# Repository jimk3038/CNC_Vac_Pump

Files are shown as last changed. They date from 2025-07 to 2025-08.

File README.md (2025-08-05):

# CNC Vacuum Pump Controller

This repo goes along with the following YouTube video:
https://youtu.be/Fw-1sRhIoUw

Update Video:
https://youtu.be/3FdK16Jd_hk

CNC Vacuum Pump Controller
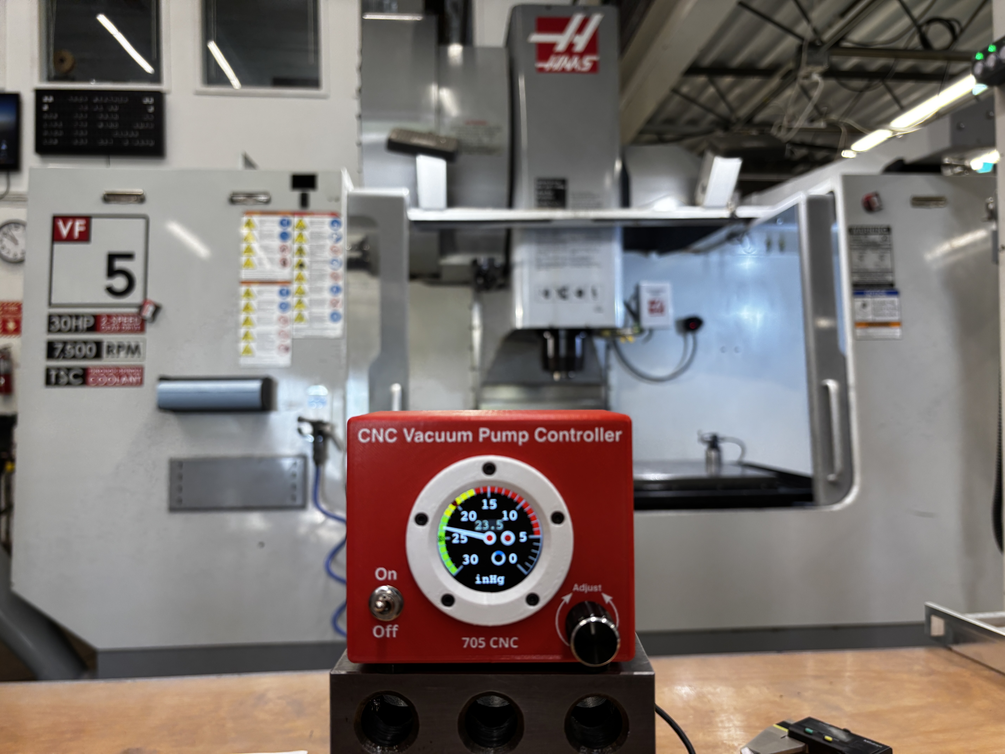
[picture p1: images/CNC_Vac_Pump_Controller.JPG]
CNC Vacuum Pump Controller


Everything needed to get up and running, in terms of CNC Vacuum plates and chucks is covered here.  Specifically, the actual vacuum pump controller is covered.

Vacuum Plate Example (see CAD/Vacuum_Plate_v2.STEP)
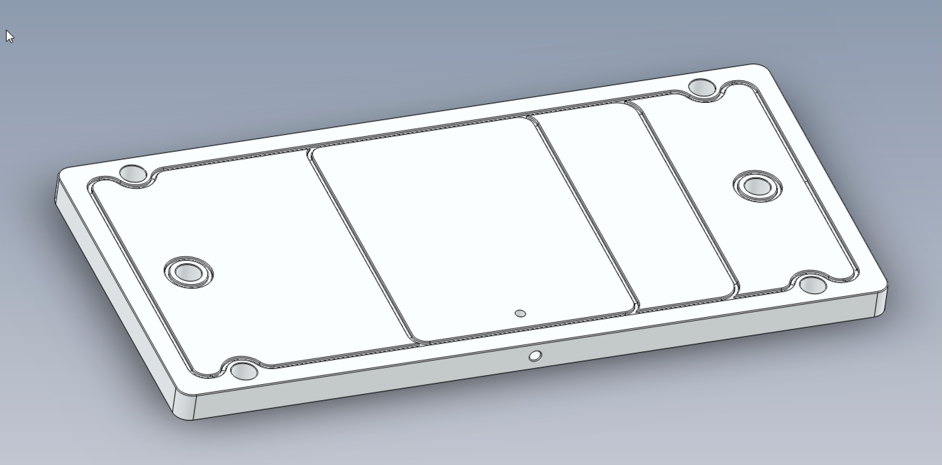
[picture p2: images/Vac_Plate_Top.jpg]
Vacuum Plate Example


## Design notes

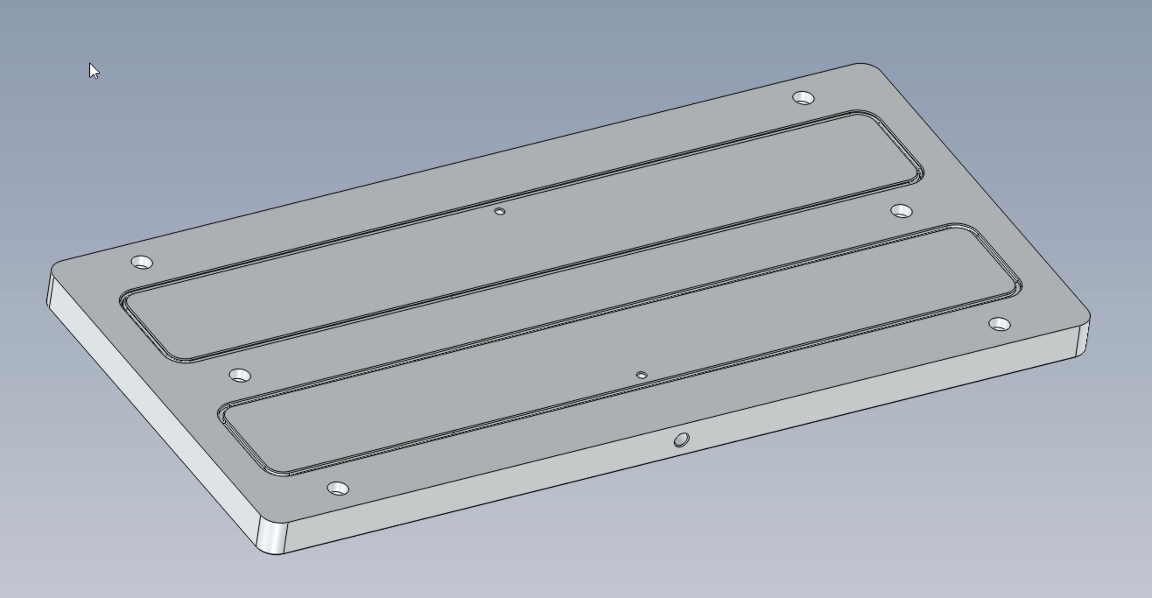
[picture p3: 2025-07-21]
images/Vac_Plate_Bottom.jpg

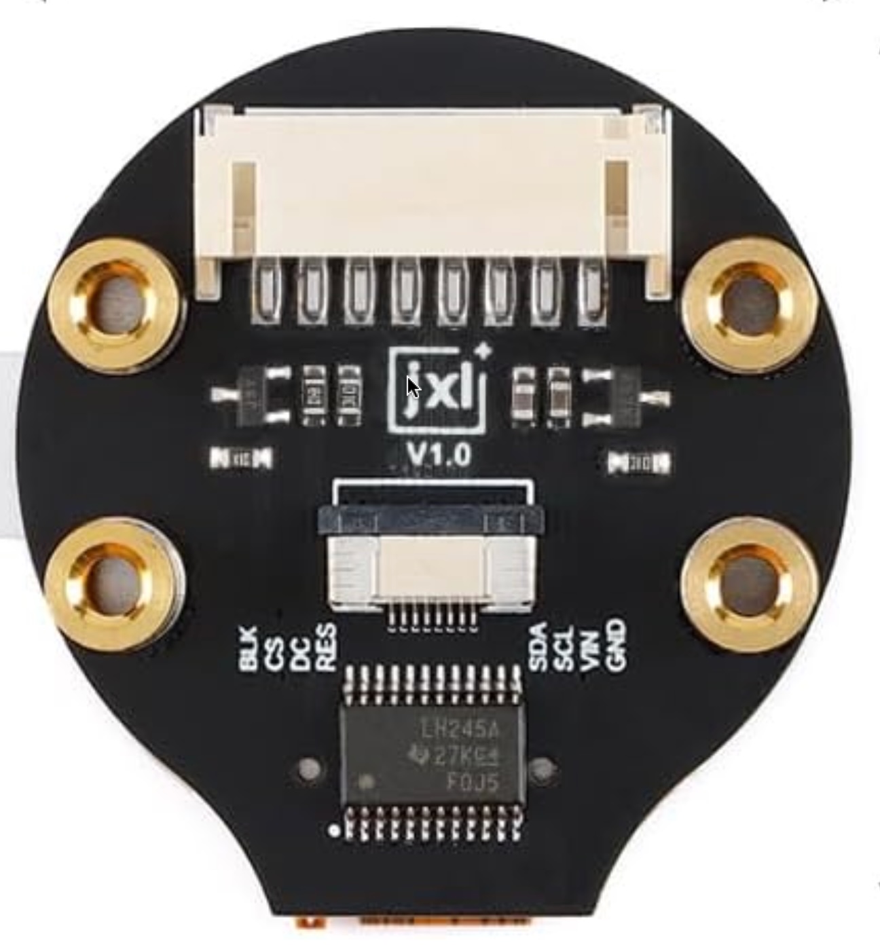
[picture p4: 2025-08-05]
images/LCD.jpg

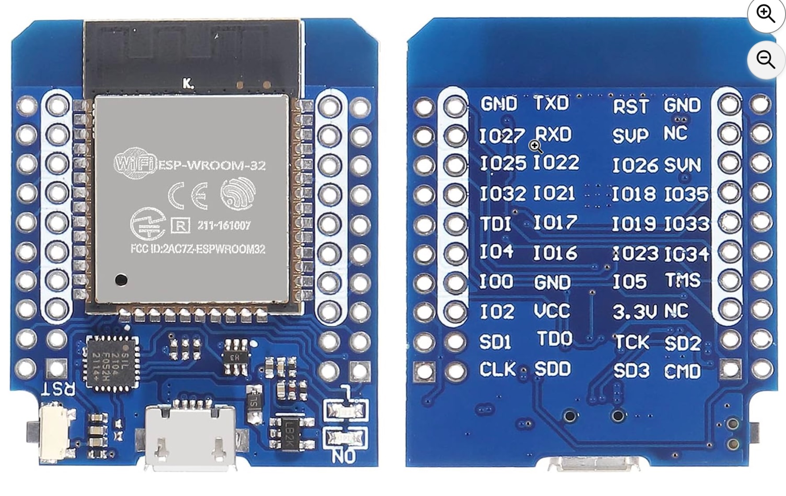
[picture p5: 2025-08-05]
images/D1_Mini32_ESP32.jpg

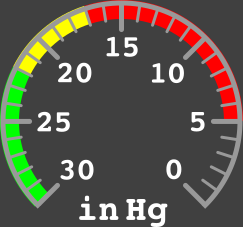
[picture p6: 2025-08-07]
source/SquareLine_VacDisp/assets/Small_Gauge_Scale_.png

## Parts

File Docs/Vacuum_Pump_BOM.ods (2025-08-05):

 | CNC Vacuum Pump Controller BOM
Supplier | Part Num | Description | Min Quantity | Unit Price | Total
Amazon | https://www.amazon.com/dp/B0CB3V1366 | LCD | 3 | $6.33 | $19.00
Amazon | https://www.amazon.com/dp/B08PNWB81Z | ESP32 | 5 | $6.00 | $30.00
Amazon | https://www.amazon.com/dp/B0C6Q67V97 | Encoder | 6 | $1.50 | $9.00
Amazon | https://www.amazon.com/dp/B07QGDDTWJ | Switch | 8 | $0.96 | $7.66
 |  | PLA Plastic | 1 | $4.00 | $4.00 | Unit Total: | $60.19
Amazon | https://www.amazon.com/dp/B00E0NTPP4 | Relay1 | 1 | $6.80 | $6.80 | Total: | $118.06
 |  | Relay2 | 1 | $8.00 | $8.00
 |  | Wire | 1 | $2.00 | $2.00
Mouser | 841-MPXV4115VC6U | Sensor | 1 | $23.10 | $23.10
 |  | Sensor Adapter Hose | 15 | $0.50 | $7.50
 |  | Printing | 1 | $1.00 | $1.00
 |  | Extra Stuff
 |  | Shopify | 1 | $6.00 | $6.00
 |  | Packaging | 1 | $2.00 | $2.00
 |  | Shipping | 1 | $5.00 | $5.00

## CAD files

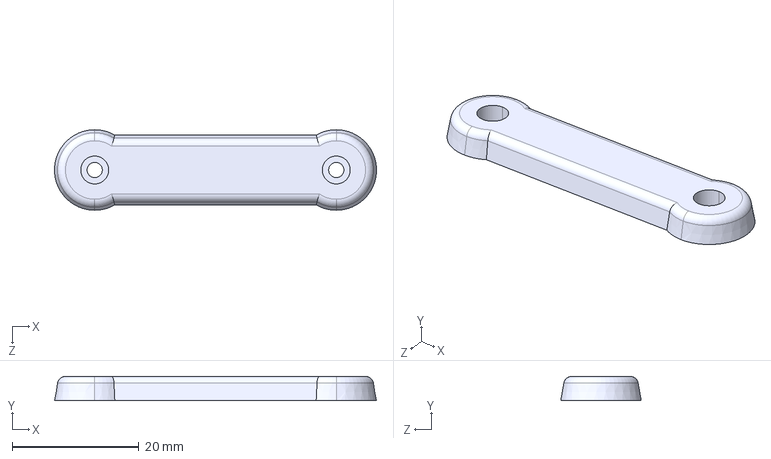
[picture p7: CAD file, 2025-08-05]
CAD/Rubber_Foot_Strip.STEP
50.8 x 3.81 x 12.7 mm

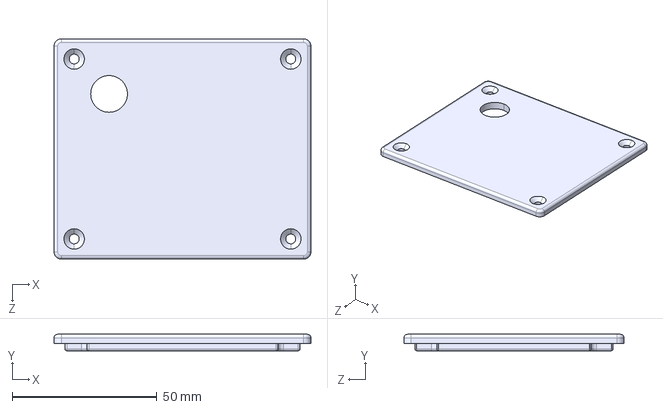
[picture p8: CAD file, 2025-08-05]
CAD/Back_Cover.STEP
88.9 x 5.71 x 76.2 mm

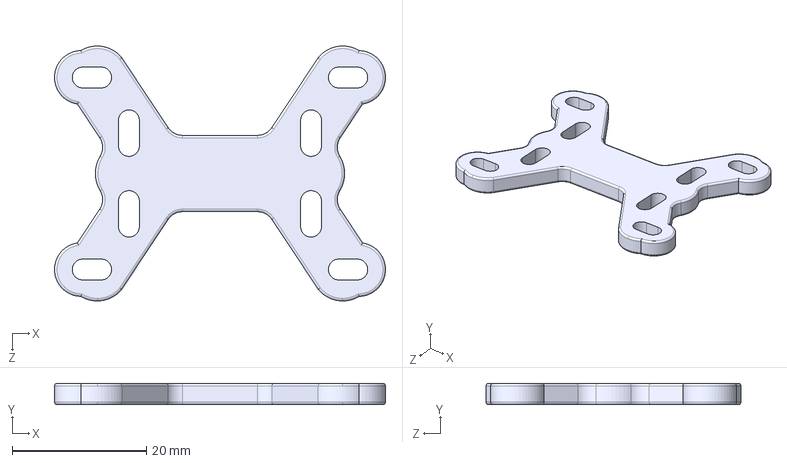
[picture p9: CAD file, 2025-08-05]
CAD/LCD_Support_JXL_.STEP
49.2 x 3.17 x 37.9 mm

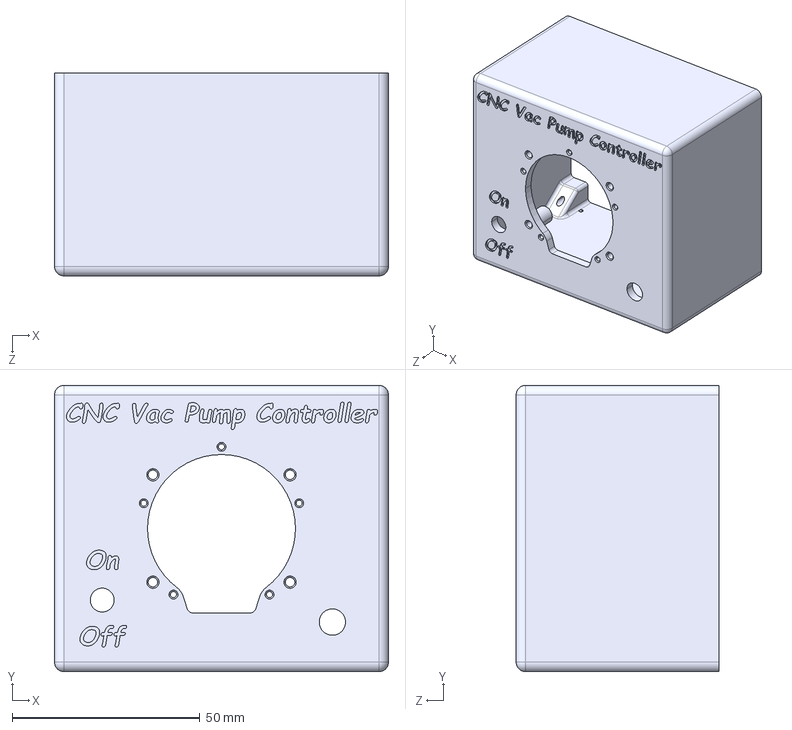
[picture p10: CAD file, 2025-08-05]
CAD/Enclosure.STEP
88.9 x 76.2 x 54.0 mm

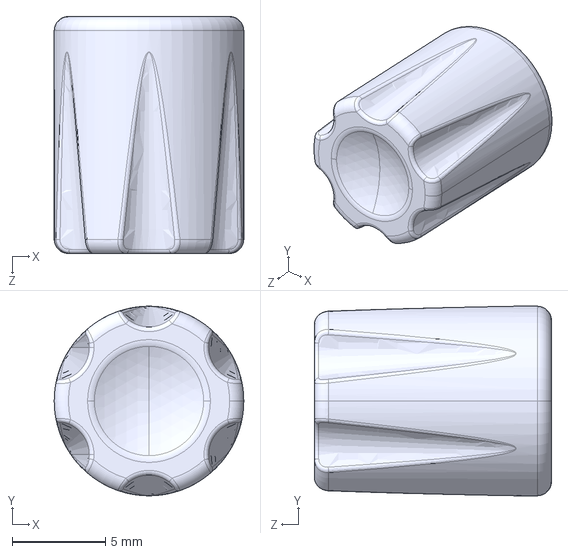
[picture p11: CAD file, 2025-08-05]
CAD/Knob.STEP
10.2 x 10.2 x 12.7 mm

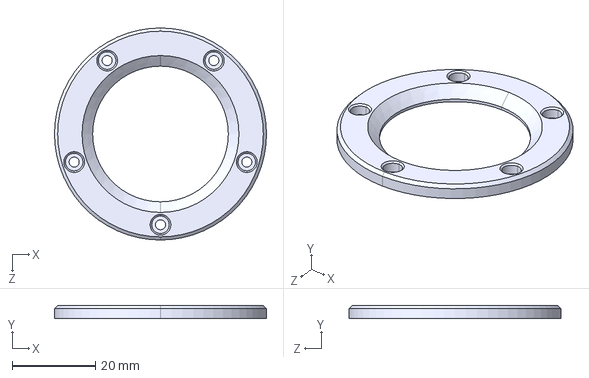
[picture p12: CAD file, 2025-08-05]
CAD/Bezel.STEP
50.8 x 3.17 x 50.8 mm

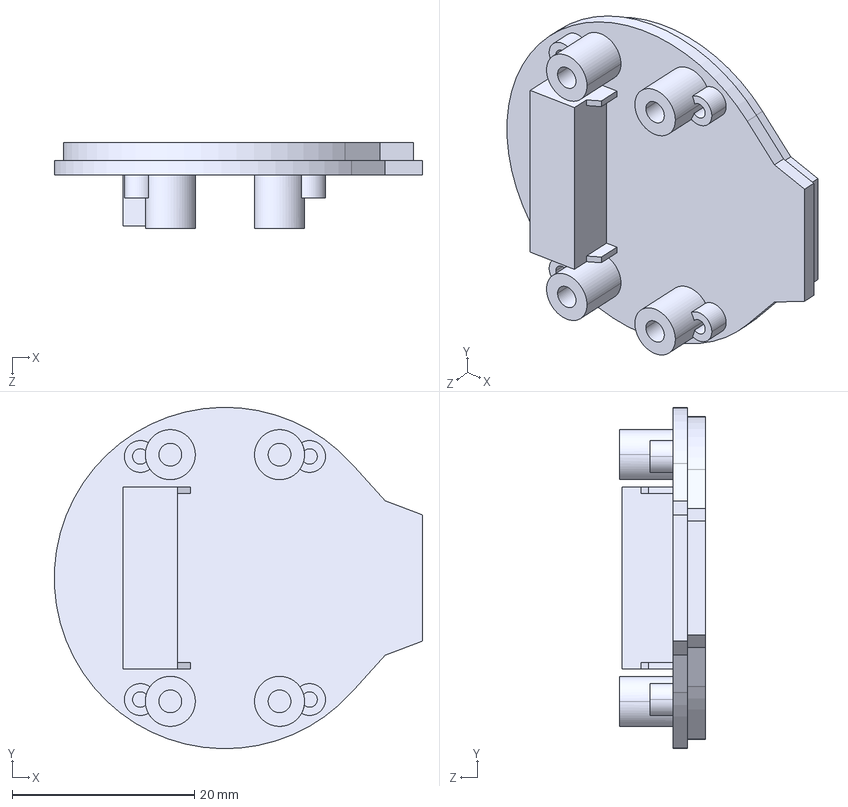
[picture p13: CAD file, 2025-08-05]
CAD/Round_LCD_1pt28in_JKL.STEP
40.4 x 37.5 x 9.50 mm

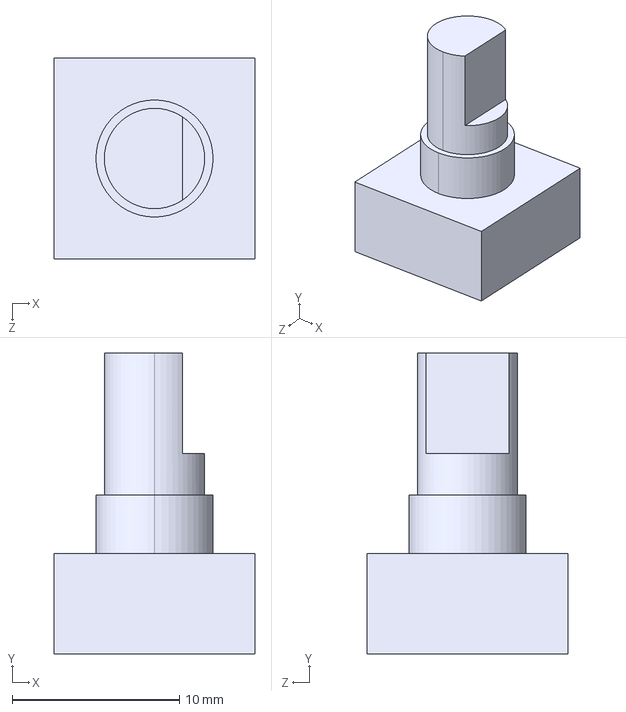
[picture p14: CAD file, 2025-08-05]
CAD/Encoder.STEP
12.0 x 18.0 x 12.0 mm

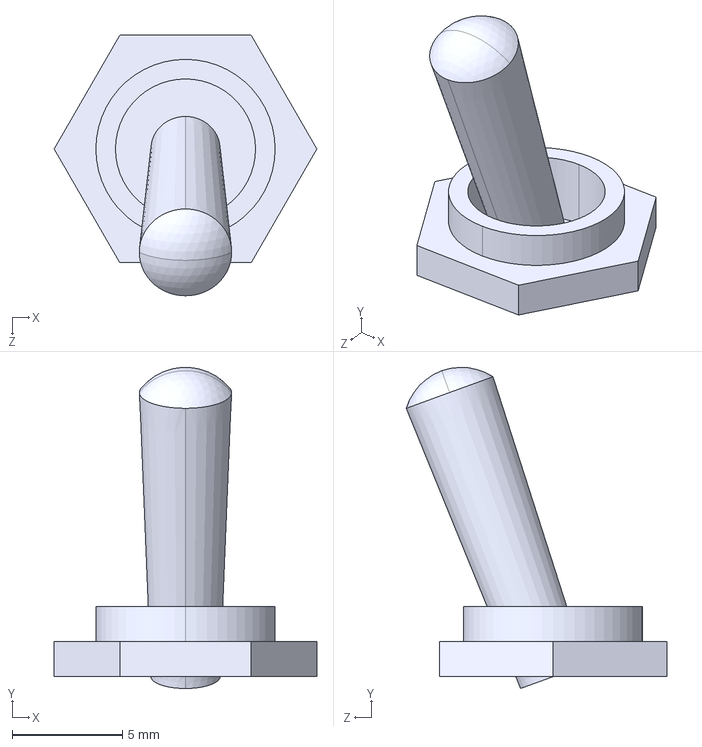
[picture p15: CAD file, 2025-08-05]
CAD/Toggle_Switch.STEP
11.9 x 14.6 x 11.8 mm

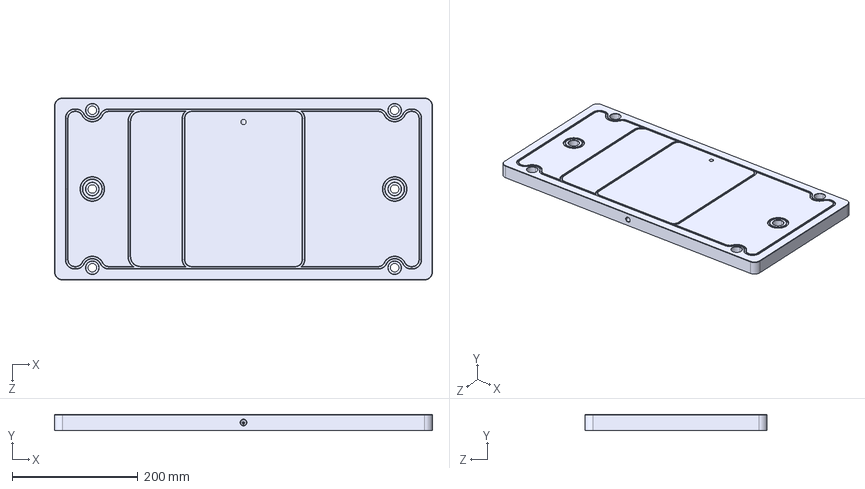
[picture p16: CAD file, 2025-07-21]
CAD/Vacuum_Plate_v2.STEP
600.1 x 25.4 x 288.9 mm

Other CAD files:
CAD/Vacuum_Plate_v2.SLDPRT

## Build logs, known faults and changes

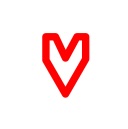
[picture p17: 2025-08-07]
source/SquareLine_VacDisp/assets/red_bug.jpg

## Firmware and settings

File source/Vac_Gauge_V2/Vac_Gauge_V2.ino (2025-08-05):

//
// CNC Vacuum Pump Controller
//
// See "notes.h" for documentation.
//

// Setup the vacuum high and low default thresholds before including "encoder.h".
// The values are in "inHg * 10".  So, a value of 200 is really 20.0inHg.
int16_t red=200, grn=250;

#include "encoder.h"

// Comment out the next line to build program WITHOUT the LCD / GUI interface.
// With the GUI, the ESP32 will just switch the pump on/off at the threshold
// points.  You will need to recompile the code to change the switch points.
#define USE_GUI

#ifdef USE_GUI
  #include <TFT_eSPI.h>
  #include <lvgl.h>
  #include "src/ui_lvgl/ui.h"

  // Waveshare 1.28in Round LCD
  static const uint16_t screenWidth  = 240;
  static const uint16_t screenHeight = 240;

  static lv_disp_draw_buf_t draw_buf;
  static lv_color_t buf[ screenWidth * 10 ];

  TFT_eSPI tft = TFT_eSPI(screenWidth, screenHeight); // TFT Instance
  lv_disp_drv_t disp_drv;
  bool guiActive = true;
#else
  bool guiActive = false;
#endif


const int ledPin = 2;             // Debug LED on ESP32 board.
const int vacSensorPin = 35;      // Analog Input Pin for Vacuum Sensor
const int sensorPwrPin = 4;       // Dummy pin provides power for Vac Sensor
const int vacPumpPin = 26;        // Output to Vacuum Pump Relay
const int vacAlarmPin = 21;       // Output to Alarm Relay

// Relays are active low.  Enum makes for a nice way to control them, I think.
enum relayType{ On = 0, Off = 1 };

uint16_t getFilteredVacSensor();
int cmpfunc (const void * a, const void * b);
void printTypes();
void startGUI();

// Timers used with millis().
uint64_t tm, lv_tm1, lv_tm2, lv_tm3, tm4;

#ifdef USE_GUI

  // LCD Display Flushing for LVGL
  // ============================================================================
  void my_disp_flush( lv_disp_drv_t *disp, const lv_area_t *area, lv_color_t *color_p ) {
      uint32_t w = ( area->x2 - area->x1 + 1 );
      uint32_t h = ( area->y2 - area->y1 + 1 );

      tft.startWrite();
      tft.setAddrWindow( area->x1, area->y1, w, h );
      tft.pushColors( ( uint16_t * )&color_p->full, w * h, true );
      tft.endWrite();

      lv_disp_flush_ready( disp );
  }

  // Use Arduino millis() as tick source.
  static uint32_t my_tick(void) {
      return millis();
  }
#endif

// ============================================================================
void setup() {
    Serial.begin( 115200 );

    pinMode( sensorPwrPin, OUTPUT );      // Dummy 3.3V to Vac Sensor
    digitalWrite( sensorPwrPin, HIGH );
    pinMode( vacSensorPin, INPUT );       // Vac Analog Sensor Input    

    pinMode( ledPin, OUTPUT );            // ESP32 Board LED
    digitalWrite( ledPin, HIGH );

    pinMode( vacPumpPin, OUTPUT );        // Outputs to dual realy board.
    digitalWrite( vacPumpPin, Off );
    pinMode( vacAlarmPin, OUTPUT );
    digitalWrite( vacAlarmPin, Off );

    xTaskCreate(
      encTask,		  // My Simple Encoder Task
      "Encoder",		// Task Name String
      10000,			  // Stack size in bytes.
      NULL,			    // Parameter passed as input of the task.
      1,				    // Priority of the task.  Higher Num = Higher Priority
      NULL);			  // Task handle.

    Serial.printf("\nCNC Vac Pump Controller:\n");
    #ifdef USE_GUI
      startGUI();     // Init and startup GUI display here.
      Serial.printf("\tLVGL: %d.%d.%d\n",
        lv_version_major(), lv_version_minor(), lv_version_patch() );
    #endif
    Serial.printf( "Setup Done\n" );

    // Init the timers so they are staggered.  This keeps them from happening 
    // at the same time.  Also, to keep the stagger working, jump the timer(s) forward 
    // on multiples of 5 milliseconds.
    tm = millis();
    lv_tm1 = tm + 1;
    lv_tm2 = tm + 2;
    lv_tm3 = tm + 3;
    tm4 = tm + 4;
}

// ============================================================================
void loop() {
  static int ang;
  char sVal[30];
  static bool ledFlg = true;
  static int cnt_old;
  static int vacSensor, vacVal;

  #ifdef USE_GUI
    // This should be moved to a high priority FreeRTOS task.
    if( guiActive && lv_tm1 < millis() ) {      
      lv_tick_inc( 5 );           // Update GUI animations.
      lv_tm1 += 5;
    }

    if( guiActive && lv_tm2 < millis() ) {
      lv_timer_handler();         // Update GUI every 5ms.
      lv_tm2 += 5;
    }
    
    // Update vacuum label and needle angle.
    if( guiActive && millis() > lv_tm3 ) {
      // lv_tm3 += 45;
      lv_tm3 += 15;
      // int vacSensor = analogRead( VAC_SENSOR );
      // vacSensor = getFilteredVacSensor();
    
      sprintf( sVal, "%0.1f", vacVal / 10.0 );
      lv_label_set_text( ui_vacLabel, sVal );

      ang = map( vacSensor, 0, 4096, 0, 2700 );
      lv_img_set_angle( ui_Needle, ang );

      // Pump On
      if( vacVal <= red )
        lv_obj_clear_flag( ui_ledRedImage, LV_OBJ_FLAG_HIDDEN );

      // Pump Off
      if( vacVal >= grn )
        lv_obj_add_flag( ui_ledRedImage, LV_OBJ_FLAG_HIDDEN );
    }

      // On encoder counts change...
    if( guiActive && cnt != cnt_old ) {
      // Serial.printf("Cnt: %d   Red: %d   Grn: %d\n", cnt, red, grn );
      // In case one bug is getting pushed by the other bug, update both bugs.
      uint16_t redBugAng = map( red, 300, 0, -1350, 1350 );
      lv_img_set_angle( ui_redBugImg, redBugAng );
      uint16_t grnBugAng = map( grn, 300, 0, -1350, 1350 );
      lv_img_set_angle( ui_grnBugImg, grnBugAng );
    }
    cnt_old = cnt;
  #endif

  // Toggle Board Debug LED - just to show some life.
  if( millis() > tm ) {
    tm += 250;
    ledFlg ^= true;                   // Toggle flag.
    digitalWrite( ledPin, ledFlg );
  }

  // Read Vacuum sensor and update the pump and alarm outputs.
  if( tm4 < millis() ) {
    tm4 += 10;
    
    vacSensor = getFilteredVacSensor();
    vacVal = map( vacSensor, 0, 4090, 300, 0 );

    if( vacVal <= red )  digitalWrite( vacPumpPin, On );
    if( vacVal >= grn )  digitalWrite( vacPumpPin, Off );

    // ToDo: Add code to drive the alarm output too.
  }
}



// Size of median filter for incoming analog values.
#define NUM_VAC_VALUES	15
#define NUM_VAC_AVG     15

// Get Filter Vacuum Sensor: Reads a new value from the analog input pis.
// The new value is added to a median filter who's output is then averaged.
// The median filter gets rid of "flyer" values, and then, the averaging
// smooths just a bit.  The downside to all this filtering, of course, is a 
// delay in seeing real changes.  In other words, it takes some time for 
// a large jump in the actual value to percolate through the filters.
// However, in this application, slow moving values are the norm!
// ============================================================================
uint16_t getFilteredVacSensor( ) {
  static uint16_t vacValuesRaw[ NUM_VAC_VALUES ];       // Ring Buffer of Raw Values
  static uint16_t vacValuesSorted[ NUM_VAC_VALUES ];    // Sorted Copy of Ring Buff
  static uint8_t vacValIndex = 0;                       // Current Index into Ring Buffer
	static uint32_t avgVac = 0;                           // Running Average
  
  // Overwritten oldest val in the ring buffer with new analog value.
	vacValuesRaw[ vacValIndex ] = analogRead( vacSensorPin );
	vacValIndex = ++vacValIndex > NUM_VAC_VALUES ? 0 : vacValIndex;   // If needed, wrap index.

	// Copy the unsorted raw values and overwrite the old sorted values.
	memcpy( vacValuesSorted, vacValuesRaw, sizeof(uint16_t) * NUM_VAC_VALUES );

	// QSort the values so we can find the 'median' value in the sorted list.
  // Note, QSort is super fast and efficient - truly magical and worth the effort.
	qsort( vacValuesSorted, NUM_VAC_VALUES, sizeof(uint16_t), cmpfunc);

  // Take the middle value from the sorted array - this is the 'median' value.
  // Compute an average of that median value to smooth it.
	avgVac = (avgVac * (NUM_VAC_AVG - 1) + vacValuesSorted[ NUM_VAC_VALUES / 2 ]) / NUM_VAC_AVG;
	return avgVac;
}

// Used by the QSort function to compare two values.
// ============================================================================
int cmpfunc (const void * a, const void * b) {
	if( *(int*)a > *(int*)b ) return 1;
	else if( *(int*)a == *(int*)b ) return 0;
	else return -1;
}

// Everything needed to startup the LCD display using TFT_eSPI and LVGL.
// ============================================================================
#ifdef USE_GUI
void startGUI( ) {

  // If USE_GUI is not defined then this function does nothing.
    lv_init();

    tft.begin();            // TFT Init
    tft.setRotation( 0 );   // No landscape or flipped needed.

    lv_disp_draw_buf_init( &draw_buf, buf, NULL, screenWidth * 10 );

    // Initialize the display
    lv_disp_drv_init( &disp_drv );
    disp_drv.hor_res = screenWidth;
    disp_drv.ver_res = screenHeight;
    disp_drv.flush_cb = my_disp_flush;
    disp_drv.draw_buf = &draw_buf;
    lv_disp_drv_register( &disp_drv );

    ui_init();
}
#endif

// // Debugging Stuff...
// // Dump how many bytes it takes to store each type on an ESP32.  Note, the 'int'
// // and 'long' use 32bits.  That's because the ESP32 is a 32bit processor so there
// // is no bonus using two bytes for an 'int'.  Also note, 'double' and 'long double'
// // are both eight bytes, which seems strange.
// // ============================================================================
// void printTypes() {
//     Serial.println("ESP32 Type Sizes:");                                  // Answers:
//     Serial.print("bool ");           Serial.println(sizeof(bool));        // 1
//     Serial.print("char ");           Serial.println(sizeof(char));        // 1
//     Serial.print("int ");            Serial.println(sizeof(int));         // 4
//     Serial.print("long ");           Serial.println(sizeof(long));        // 4
//     Serial.print("long long ");      Serial.println(sizeof(long long));   // 8
//     Serial.print("float ");          Serial.println(sizeof(float));       // 4
//     Serial.print("double ");         Serial.println(sizeof(double));      // 8
//     Serial.print("long double ");    Serial.println(sizeof(long double)); // 8
// }

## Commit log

2025-07-21 Update README.md
    Added section for vacuum plate.
2025-07-21 Create vac_plate_example.jpg
    Image of vacuum plate.
2025-07-21 Add images of vacuum plate example.
2025-07-21 Added CAD for Vac Plate Example
    [Vacuum_Plate_v2.SLDPRT, Vacuum_Plate_v2.STEP]
2025-08-05 Added Vac Pump Controller image.
2025-08-05 Added CAD Step Files
    [Back_Cover.STEP, Bezel.STEP, Enclosure.STEP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]
2025-08-05 Added Docs
    [Vacuum_Pump_BOM.ods]
2025-08-05 Added KiCad PCB Files
    [Vac_Pump_Controller.kicad_pcb, Vac_Pump_Controller.kicad_sch]
2025-08-05 Added ESP32 source code.
